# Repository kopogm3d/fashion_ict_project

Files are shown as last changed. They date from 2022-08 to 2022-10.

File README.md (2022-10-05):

# 피팅봇

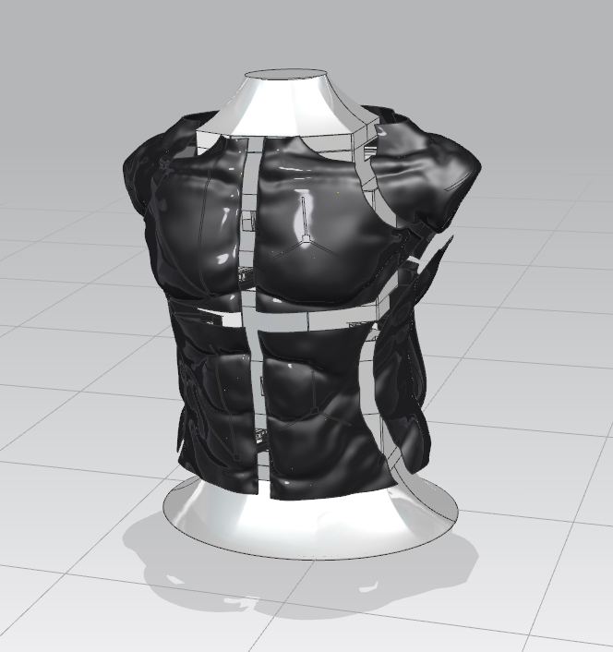
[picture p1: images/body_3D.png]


피팅봇은 하드웨어 기반의 Fashion 산업과 IT 기술 산업의 융합형 project 입니다.

##  개요 

피팅봇은 `스마트 피팅 로봇`으로  인체 치수를 입력하면, 해당 크기로 모습이 변형되는 마네킹입니다. 

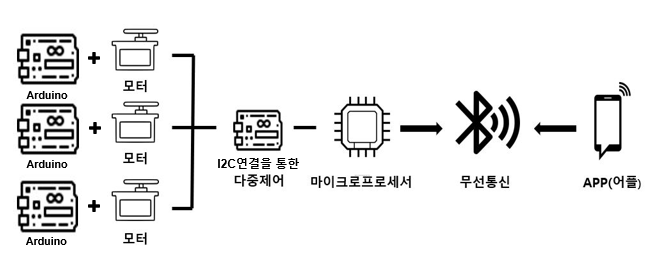
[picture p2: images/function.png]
이미지2


* PRT 모델링 및 STL 출력파일
* 아두이노 Master - Slave 동작코드
* Serial Monitor 및 중앙 제어 시스템

##  주요 제품기능

####  01. 마네킹 기둥설계

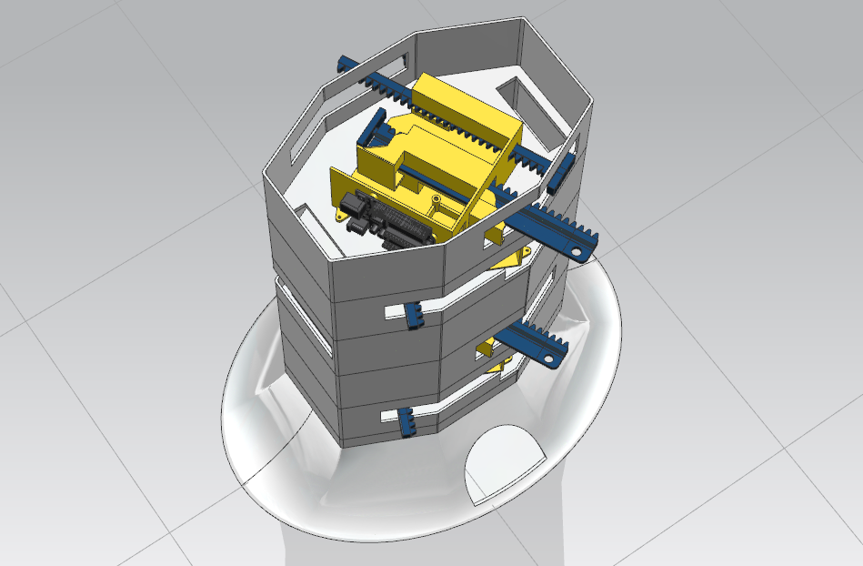
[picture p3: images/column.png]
이미지3

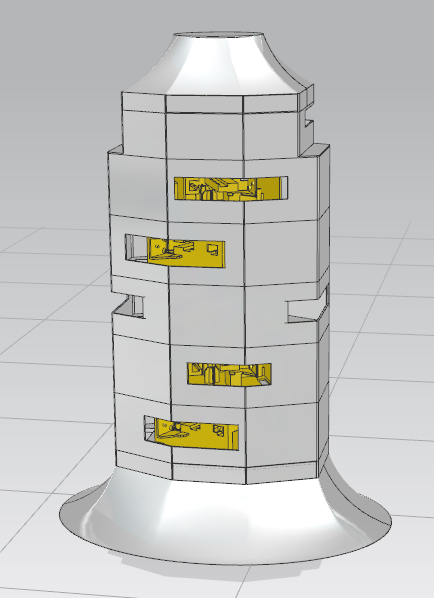
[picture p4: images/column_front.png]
이미지4

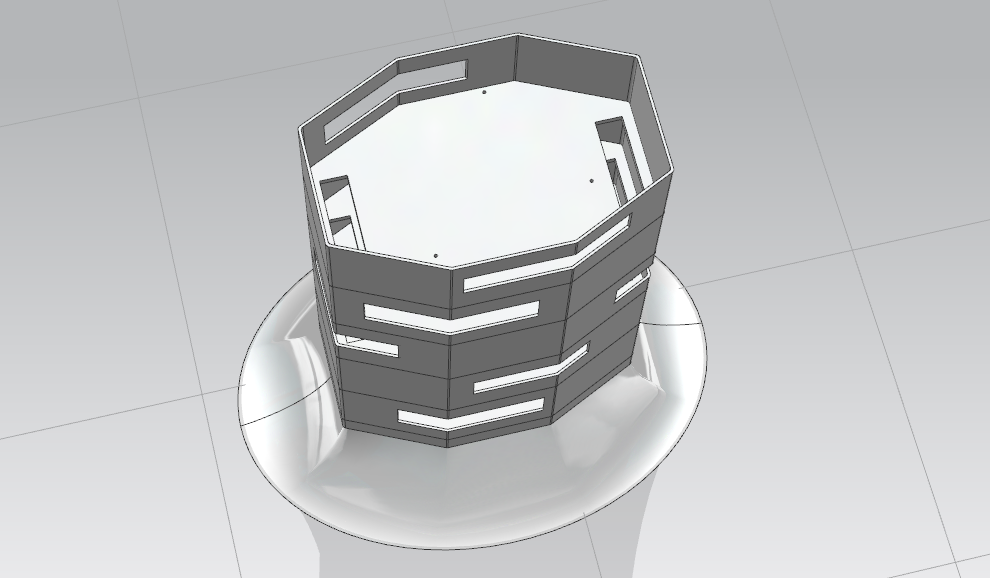
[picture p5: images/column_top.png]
이미지5


6개의 층으로 구성된 기둥을 설계하여 각 층에 모듈을 부착합니다.

####  02. 마네킹 조각 설계

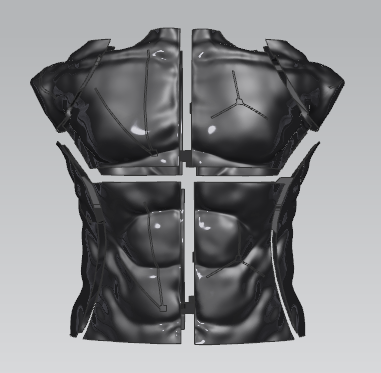
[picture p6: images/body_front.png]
이미지6

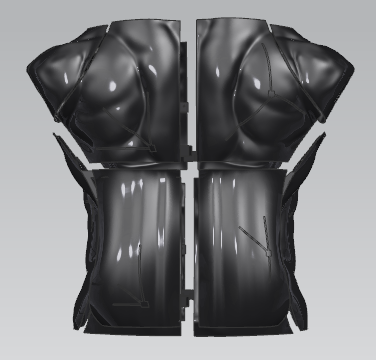
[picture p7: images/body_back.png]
이미지7


신체 형상(상체)은 12 조각으로 나누어 작동시킵니다.

####  03. 랙과 기어 설계

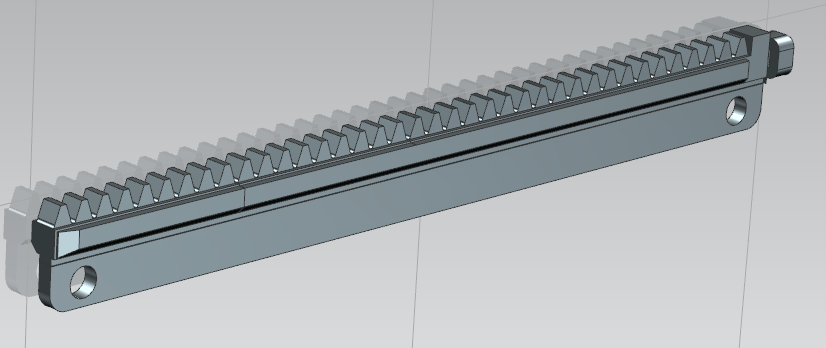
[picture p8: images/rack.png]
이미지8

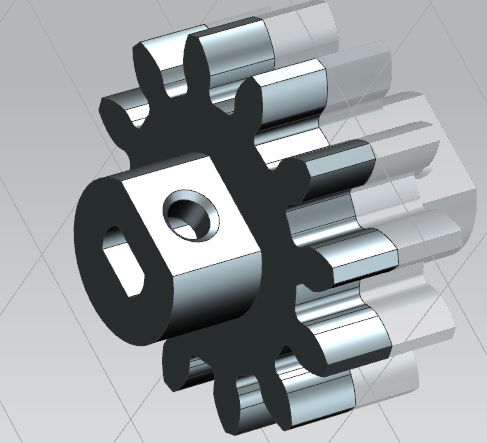
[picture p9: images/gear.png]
이미지9


####  04. 양방향 모듈 설계

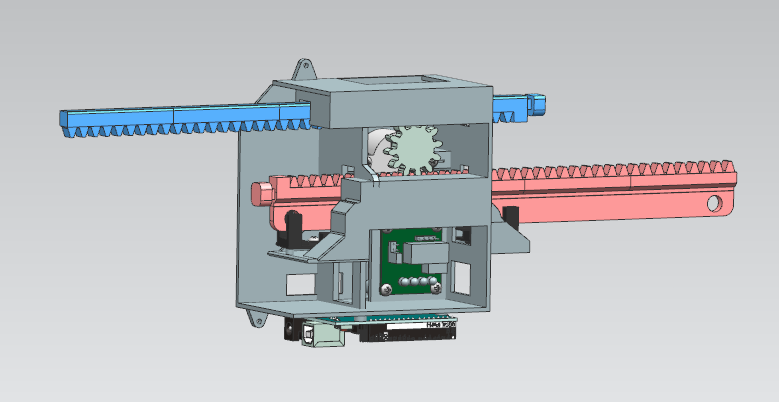
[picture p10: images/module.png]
이미지10

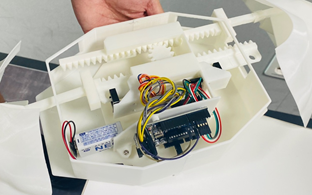
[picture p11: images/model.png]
이미지11


* 스텝모터, 모터 드라이버, 아두이노, 랙과 피니언 기어를 장착시킬 하나의 표준화된 모듈을 설계하여
어떠한 형상의 로봇이든 활용할 수 있습니다.
* 하나의 모터로 두개의 랙 및 조각을 움직일 수 있어 효율적입니다.

####  05. 앱인벤터로 인터페이스 제작

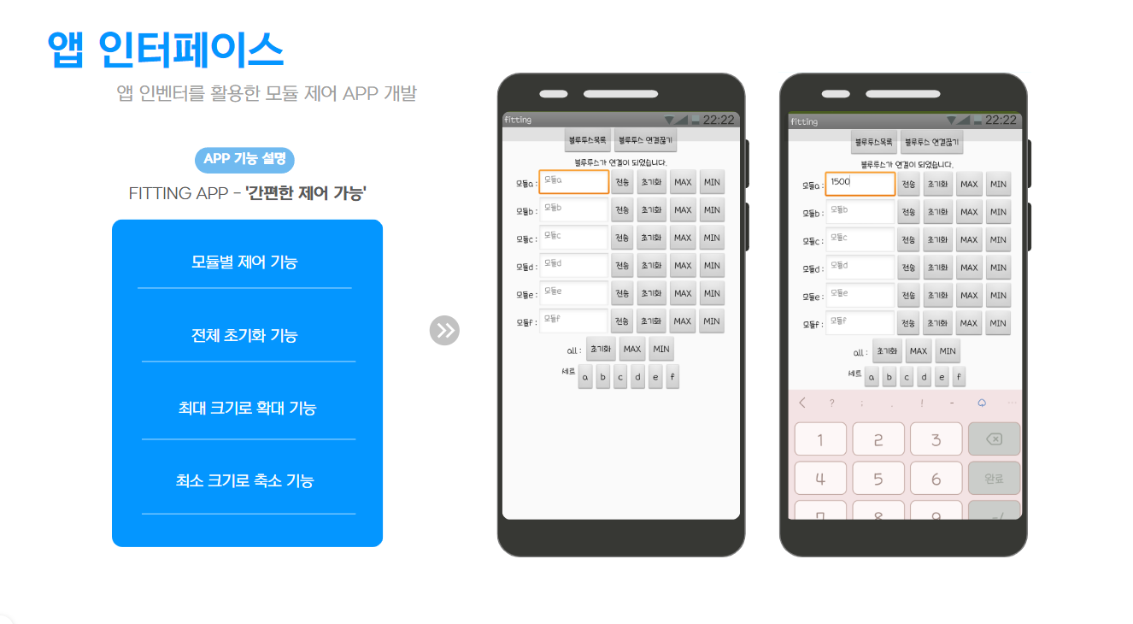
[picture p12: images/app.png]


##### - 앱 사용법
1) 블루투스 목록 및 연결 끊기 기능을 이용해 아두이노와 연결합니다.
2) 모듈을 선택 후 신체 치수를 입력하면 모터가 작동하여 해당 치수만큼 랙이 이동합니다.
3) 최대, 최소 버튼을 이용해 형상을 최대화, 최소화 시킬 수 있습니다.
4) 초기화 버튼을 통해 전체 모듈을 초기값으로 되돌립니다.

##  기술 스택

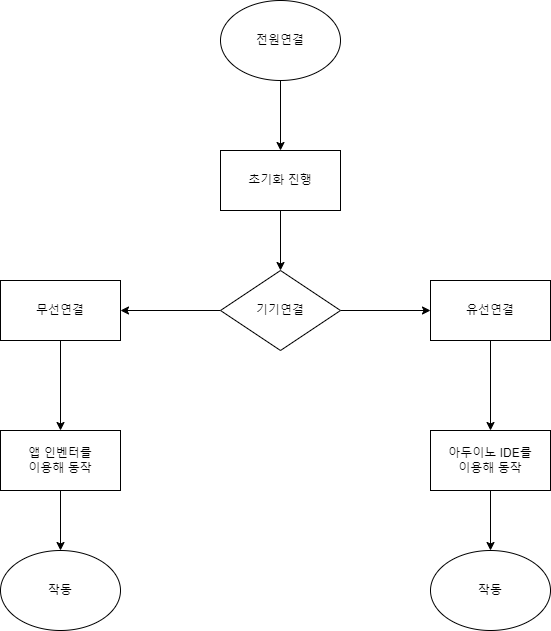
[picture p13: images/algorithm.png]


#####  - 작동 순서

1. 유/무선 연결
-  무선연결 : 블루투스 센서를 이용하여 모바일기기와 연결합니다.
-  유선연결 : 제한된 상황에 대비하여 유선연결을 지원합니다.

2-1. 치수입력
- 사용자가 신체 치수를 입력합니다.
- 유선연결의 경우엔 사용자가 모듈을 선택하는 값을 입력합니다.
- 무선연결 앱 사용자의 경우 미리 정의된 모듈의 텍스트박스 안에 수치를 입력 후 적용버튼을 클릭합니다.

2-2. 저장된 값 불러오기
- 본인이 저장한 수치값을 불러올 수 있습니다.

3. 모터작동
- 불러온 치수데이터를 기반으로 모터를 해당 값만큼 동작시킵니다.

4. 피팅더미의 크기조절
-  모터의 작동을 통해 크기를 축소, 확대 할 수 있습니다.

5. 초기화
-  포토센서를 통한 끝 렉의 끝값을 검출하는 과정을 통해 피팅더미를 초기값으로 되돌립니다.

## 작품 실물 사진

이미지1
이미지1

##### 3D 프린터로 출력한 기둥 및 조각 사진

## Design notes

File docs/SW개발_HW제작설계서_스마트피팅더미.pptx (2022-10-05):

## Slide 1

내가 기획한 ICT가
세상을 바꾼다면?

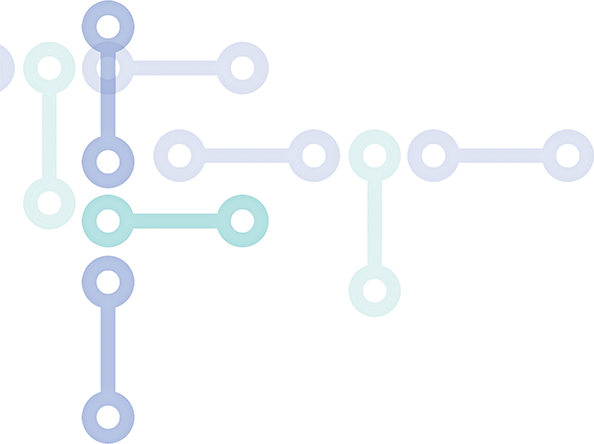
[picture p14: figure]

SW개발/HW제작 설계서

프로젝트 명 : 스마트 피팅 더미

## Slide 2

| 시장/기술 동향 분석

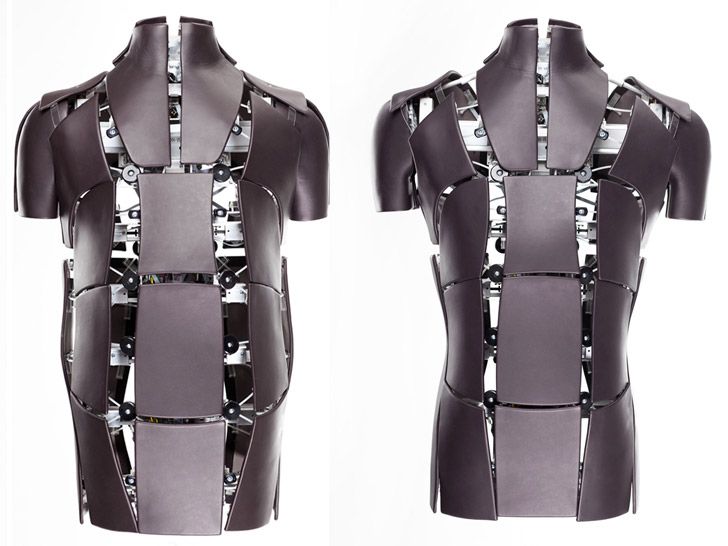
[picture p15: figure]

디자이너가 의류 제작 시 스마트피팅더미 하나만으로 다양한 체형 별 옷사이즈를 직접 눈으로 확인하고 제작할 수 있기에 제작자의 편의를 높임.

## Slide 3

시장/기술 동향 분석

소비자들을 위한 편리한 의류 구매환경 조성 필요

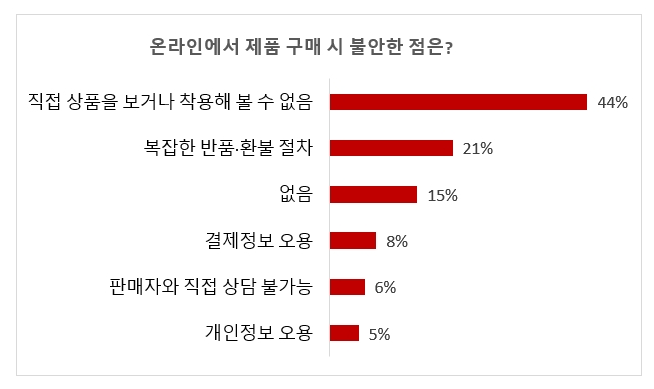
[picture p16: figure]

소비자가 의류 구매 시 매번 직접 착용해볼 수 없기에 불편함을 느낌

디자이너도 의류 제작 시 소비자의 모든 사이즈를
직접 눈으로 확인하는데 불편함이 있음

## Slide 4

| 시장/기술 동향 분석

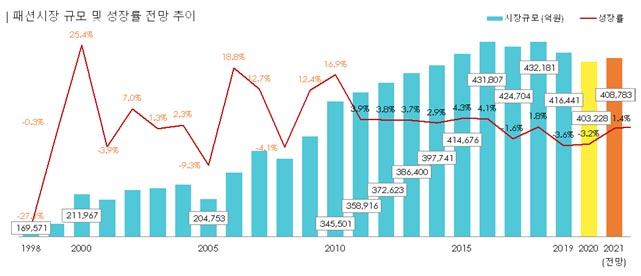
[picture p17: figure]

국내 패션시장의 규모가 점점 성장하고 있으며,
앞으로도 점점 상승할 것으로 전망됨.

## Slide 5

| 요구사항 정의서

구분 | 기능 | 설명
S/W | 수동 치수기입 | 사용자가 입력한 치수를 아두이노로 입력 받는다.
| 해당 수동 치수 저장 | 아두이노로 입력 받은 치수데이터를 저장시킨다.
| 저장된 치수 불러오기 | 저장된 치수 데이터 값을 불러온다.
| 아두이노와 모터간 통신테스트 | 초기화 코드로 통신을 테스트한다. 기반으로 모터를 작동시킨다
| 블루투스 연결을 통한 pc와 피팅더미 통신 | 저장된 치수데이터를 블루투스 기능을 통해 피팅더미를 원격으로 작동시킨다.
| 제한된 상황을 대비한 유선연결 지원 | 무선통신이 안되는 상황을 대비하여 유선연결을 가능하게 한다.

구분 | 기능 | 설명
H/W | 기어,랙 | 사이즈를 최대한 줄인 기어를 사용하고 신체 최대 치수에 맞춘 랙을 사용한다.
| 블루투스 무선통신 | 블루투스 센서를 이용하여 피팅더미와 연결한다.
| 스탭모터 | 360도 회전이 가능한 스탭모터를 사용한다.
| 더미 신체 조각 | 랙과 신체조각을 결합하고, 모터를 통해 랙을 움직여 조각의 위치를 조절한다.
| 아두이노 | 기기로부터 데이터를 송신받아 모터를 움직인다.
| 모터 드라이버 | 아두이노만으로 다량의 모터를 제어하기엔 전력과 포트의 제한이 걸리므로 모터 드라이버를 경유하여 전력을 공급한다.
| SMPS (Switching Mode Power Supply) | 아두이노에 220AC 전력을 12V로 변환시킨다.

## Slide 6

| 시스템 구성도

- 치수 입력
- 사용자의 신체 치수 입력 받는다.
- 유/무선 연결
- 유선이나 블루투스를 통해 아두이노와 사용자기기를 유/무선으로 연결한다.
- 입력 받은 치수 저장
- 저장되어 있는 치수 데이터 값 불러옴
- 저장된 데이터 불러오기
- 저장되어 있는 치수 데이터 값을 불러옴
- 초기화
- 피팅 더미를 초기값으로 되돌린다.
- 치수조절
- 마네킹조각에 연결되어 있는 모터를 이용하여 저장되어 있는 데이터 값을 기반으로 마네킹의 크기를 조절

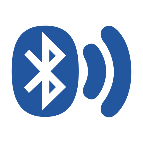
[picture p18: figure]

무선통신

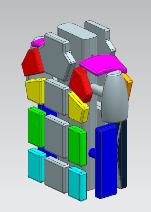
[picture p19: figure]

제작한 마네킹
조각에 모터 부착

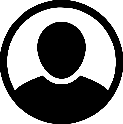
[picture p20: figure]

치수입력

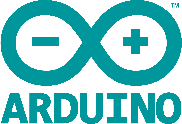
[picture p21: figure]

모터 제어

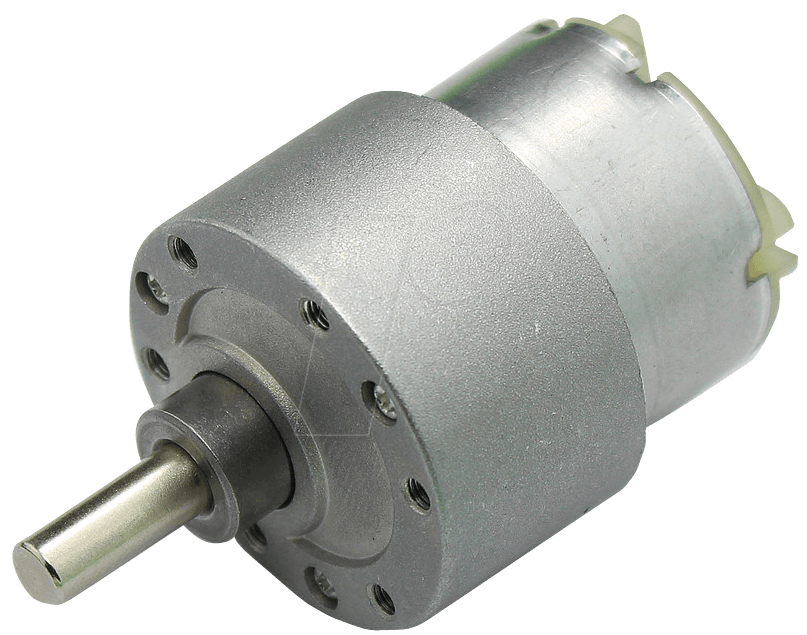
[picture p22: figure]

저장된 치수 불러오기

입력 받은
치수저장

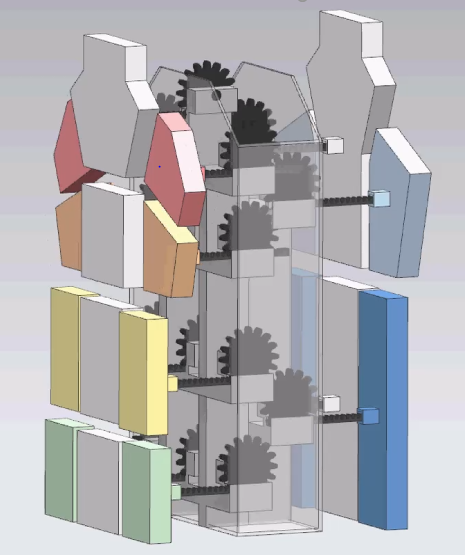
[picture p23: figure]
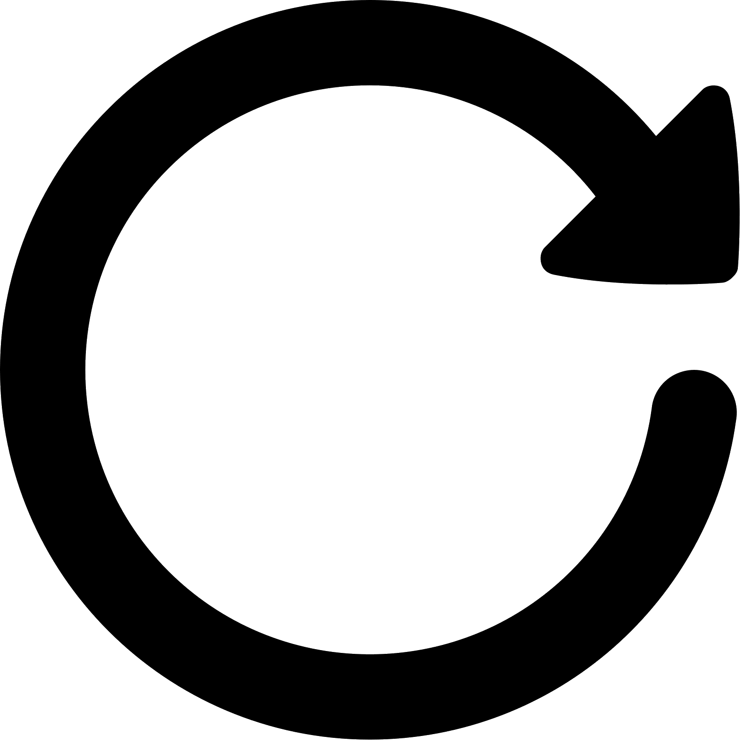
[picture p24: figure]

초기화

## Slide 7

| 하드웨어/센서 구성도

센서종류 | 연결핀 | 설명
Arduino UNO | GND | Step Motor GND에 연결
| VCC | Step Motor VCC에 연결
| Step Motor | Step Motor 신호연결 [2,3,4,5]
| Sensor | Photo Sensor 신호연결 [7,8]
| I2C | 다수기기 통신을 위해 I2C연결 [A4,A5]
| Blue Tooth | 마스터아두이노 블루투스 연결 [2,3]
Step Motor Driver | GND | Arduino – 부 연결
| VCC | Arduino + 부 연결
| Signal | [2,3,4,5] 핀연결
Battery | GND | SMPS – 부 연결
| VCC | SMPS + 부 연결

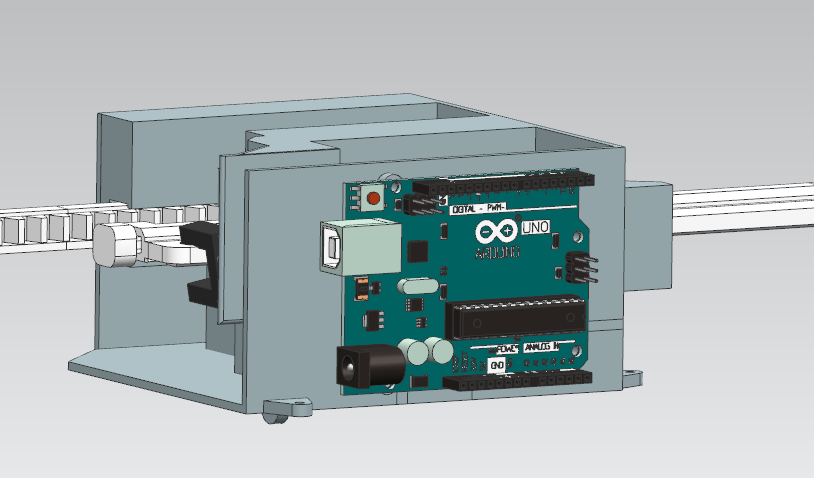
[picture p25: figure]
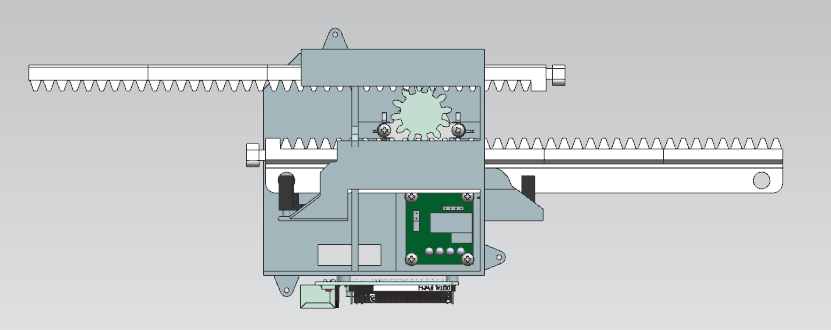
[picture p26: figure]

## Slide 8

| 메뉴 구성도

자동수치

수치입력

수동수치

적용

수치
불러오기

무선
연결

메인 화면

유/무선
연결

기기검색

유선
연결

초기화

초기값으로 적용

웹 연결

웹사이트로 이동

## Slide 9

| UI/UX 정의서 - 화면 설계서

- 제품 사용 프로그램> 수치 입력하기 > 원하는 정보 입력 > 적용

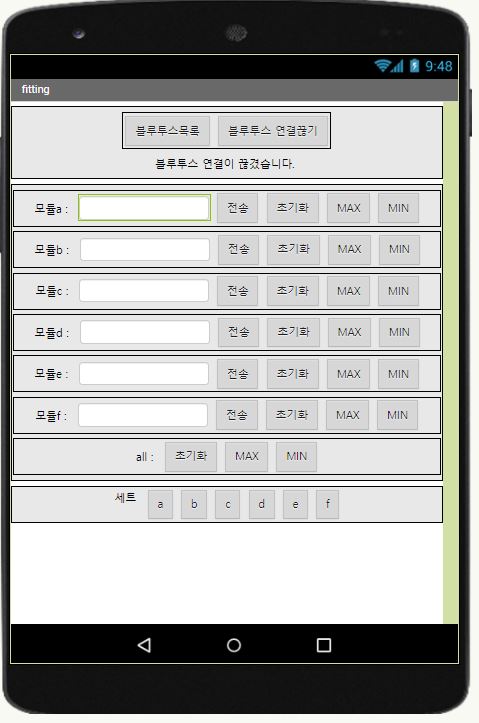
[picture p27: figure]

| 리스트 참고
1 | 평균블루투스 연결하기 연결이 안된 경우 블루투스 목록을 통해 기기를 검색할 수 있고, 연결할 수 있다.
2 | 텍스트박스 텍스트박스에 값을 입력한다.
3 | 모듈동작 전송을 통해 아두이노로 값을 전송하여 모듈을 동작시킨다.
3 | 미리정의된 수치값/ 수치 저장,불러오기 미리 초기화와 최대,최소값을 정의하여 UI화 시켰다. 그외 세트칸에 본인이 원하는 치수를 저장, 불러올 수있다.

[연결이 안된경우 블루투스목록을 통해
기기를 검색하여 연결할 수 있다.]

1

텍스트 박스안에 사용자가
동작하길 원하는 값을 입력할 수 있다.

2

텍스트 입력한 모듈위치의 전송버튼
클릭 시 입력한 값만큼 동작한다.

그외 초기화, 최대값, 최소값을
미리정의하여 지원한다.
아래 세트를 통해 사용자가 원하는
수치를 저장할 수 있다.

3

4

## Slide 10

| 화면 설계서

▶ 기능정보
기능명 | 수치 입력하기
기능설명 | 미리 정의 되어있는 값 이나, 커스텀 값을 통해 모터를 제어 할 수 있다.
처리내용 | 앱이나, 아두이노 시리얼을 통해 모듈을 동작할 수 있다. 텍스트박스에 값을 입력하여 동작할 수 있으며, 수치를 저장,불러오는 것이 가능하다.
관련번호 | -

▶ 사용 예시 정보
| 설명 | 사용자가 동작하길 원하는 수치를 선택하고 전송을 누르면 모듈이 동작한다.
| 입력 데이터 값 | 사용자가 직접 값을 입력할 수 있으며, 값을 저장, 불러올 수 있다. 초기화값과, 최대, 최소값은 미리 정의되어 불러오는 것이 가능하다.

▶ 선행필수기능 및 예외사항
기능명 / 예외사항 | 설명
한 부위만 적용한 경우 | 해당부위만 작동하여 움직인다.
최소/최대값을 초과한 경우 | 최소/최대값을 넘기면 포토센서에 걸려 그 이상 동작하지 않는다.

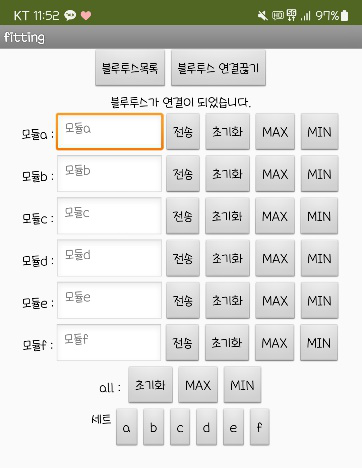
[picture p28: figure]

▶ 입출력 데이터 항목
입출력구분 | 항목 | 설명
입력 | 초기화, 최소 ,최대, 수동입력수치 | 미리 지정해둔 값과, 수동입력 값을 입력
출력 | 기기 작동 | 입력한 수치만큼 모터 작동

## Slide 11

알고리즘 명세서/설명서

실무 산출물 형식

프로그램 ID | - | 프로그램 명 | 모터제어 프로그램 | 작성일 | 22 . 10 . 5 . 수 | Page | -
개요 | 윈도우에서 pc를 통해 이두이노에 값을 입력받고 아두이노에서 모터에 신호를 보내 피팅더미를 움직인다. | | | | | 작성자 | 이동희

1. 유/무선 연결
- 무선연결 : 블루투스 센서를 이용하여 모바일기기와 연결한다.
- 유선연결 : 제한된 상황에 대비해. 유선연결을 지원한다.
2-1. 치수입력
- 사용자가 신체 치수를 입력한다.
- 유선연결의 경우엔 사용자가 모듈을 선택하는 값을 입력해준다.
- 무선연결 앱 사용자의 경우 미리 정의된 모듈의 텍스트박스 안에 수치를 입력 후 적용버튼을 누른다.
2-2. 저장된 값 불러오기
- 본인이 저장한 수치값을 불러올 수 있다.
3. 모터작동
- 불러온 치수데이터를 기반으로 모터를 해당 값만큼 동작시킨다.
4. 피팅더미의 크기조절
- 모터의 작동을 통해 크기를 축소, 확대 할 수 있다.
5. 초기화
- 포토센서를 통한 랙의 끝값을 검출하는 과정을 통해 피팅더미를 초기값으로 되돌린다.


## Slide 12

| 기능 처리도(기능 흐름도)

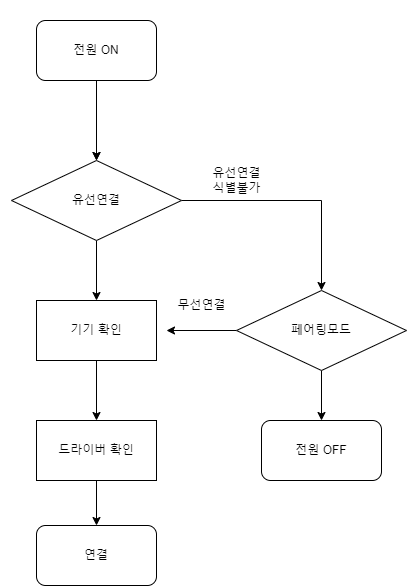
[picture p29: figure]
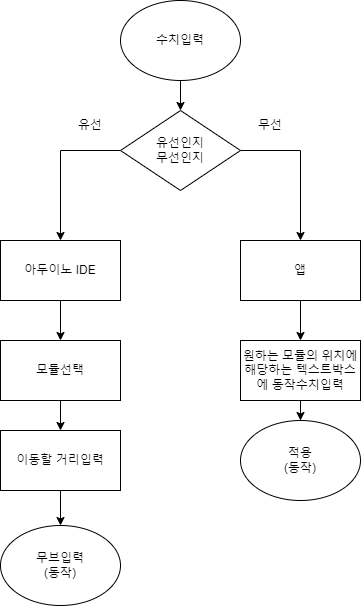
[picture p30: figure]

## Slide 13

| 핵심소스코드

2

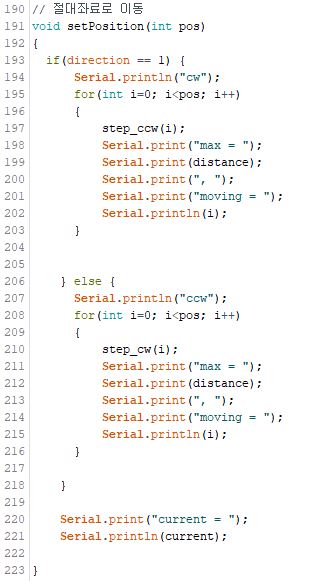
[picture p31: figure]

3

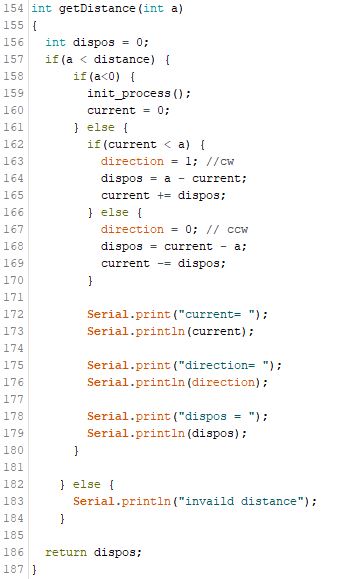
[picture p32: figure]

1.모듈선택소스코드(ASCII)
2.값을 입력받는 코드
3.입력된 값으로 모터에 전송

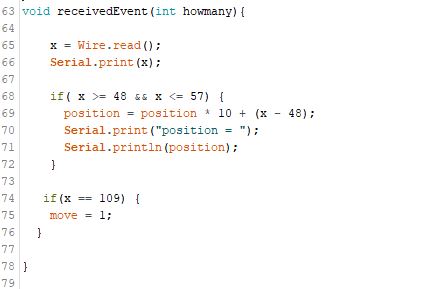
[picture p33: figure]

1

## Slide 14

| 프로그램 - 목록

기능 분류 | 기능번호 | 기능 명
PWR (POWER) | PWR-01 | 전원 ON
| PWR-02-01 | 유선연결
| PWR-02-02 | 페어링모드
| PWR-03 | 기기확인
| PWR-04-01 | 연결
| PWR-04-02 | 전원 OFF
FVR (FAVORITE) | FVR-01-01 | ALL – 초기화
| FVR-01-02 | ALL – MAX
| FVR-01-03 | ALL – MIN
A_MD (A-module) | A_MD-01-01 | A - 전송
| A_MD-01-02 | A – 초기화

한이음 ▶ 프로그램 설계서

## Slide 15

| 참조- 개발 환경 및 설명

구분 | | 항목 | 적용내역
S/W 개발환경 | 윈도우/안드로이드/IOS 조작 프로그램 개발 | App Inventor | 윈도우/안드로이드/IOS에서 수치값을 입력받는 프로그램 개발을 위해 사용한다.
| 아두이노 동작 프로그램 개발 | Arduino | 피팅더미 내부의 아두이노를 실행시키기 위해 사용한다.
| 에뮬레이션 프로그램 | Remote Testkit | 다양한 앱 환경에서 사용시 호환성 테스트를 위해 사용한다.
H/W 구성장비 | 아두이노 | 피팅더미 통신디바이스 (SZH-EK080) | 피팅더미 내부의 아두이노를 통해 모터를 동작한다.
| 스탭모터 | 조각이동을 위한 모터 (28byj) | 아두이노로 부터 값을 받아서 모터를 동작하여 랙을 동작인다.
| 모터 드라이버 | 다수의 모터제어 (ULN2003) | 대량의 모터가 들어감으로 모터드라이버를 경유하여 전력을 공급한다.
| 블루투스 송-수신기 | 블루투스 통신모듈 (SZH-EK105) | 아두이노에 블루투스 기능을 추가하여 다양한 기기와 통신을 가능하게 한다.
| 기어 & 랙 | 자체 제작 및 생산 예정 | 랙과 기어를 이용하여 피팅더미 조각을 움직인다.

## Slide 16

내가 기획한 ICT가
세상을 바꾼다면?

Thank you

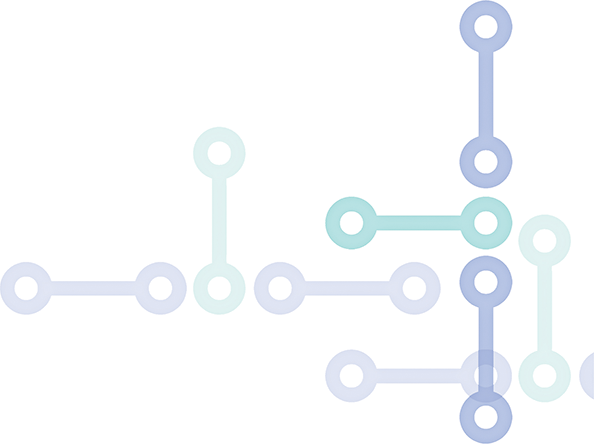
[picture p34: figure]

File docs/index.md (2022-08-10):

# 프로젝트

## 일정관리

[일정관리](https://docs.google.com/spreadsheets/d/1b1e-LViBpw9x0WHoBi6NbNIejE0as57JXm7uGB9Ble4/edit?usp=sharing)
[공유문서](https://drive.google.com/drive/folders/1tGMNQquNc3pgP5mi_j5m_SsK1CPc5LEh?usp=sharing)

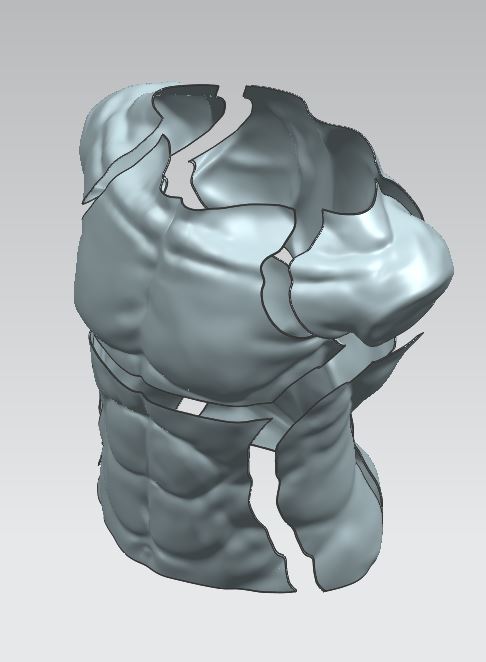
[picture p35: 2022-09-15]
images/piece.JPG

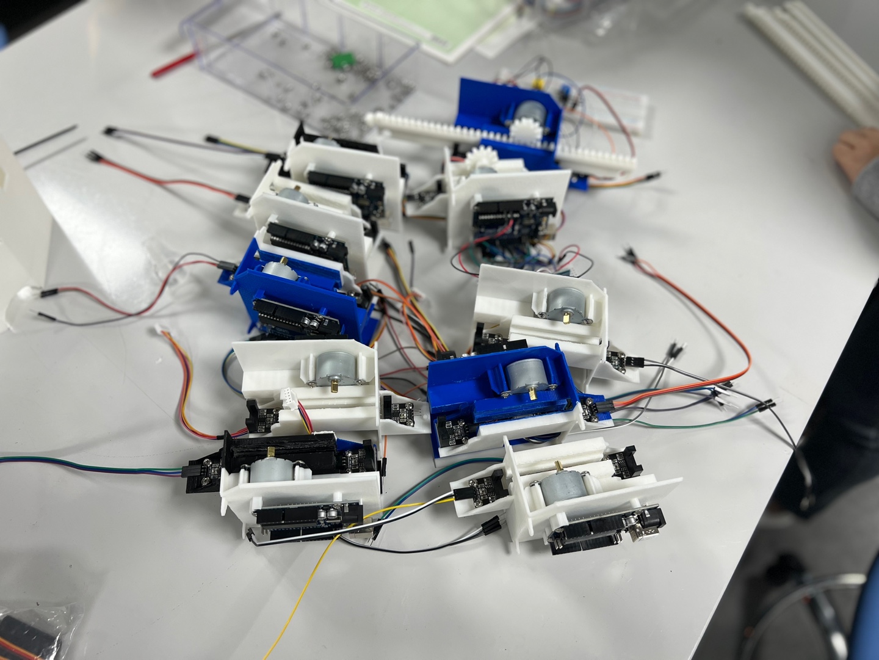
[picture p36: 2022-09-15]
images/KakaoTalk_20220906_184110311_02.jpg

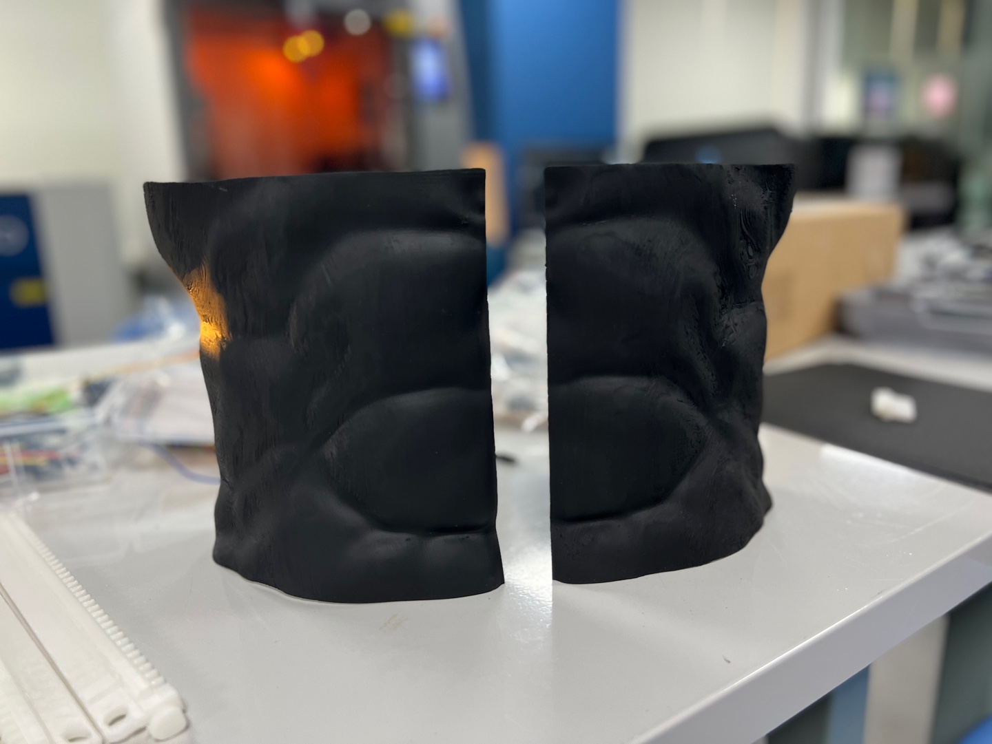
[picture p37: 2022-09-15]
images/KakaoTalk_20220906_184110311.jpg

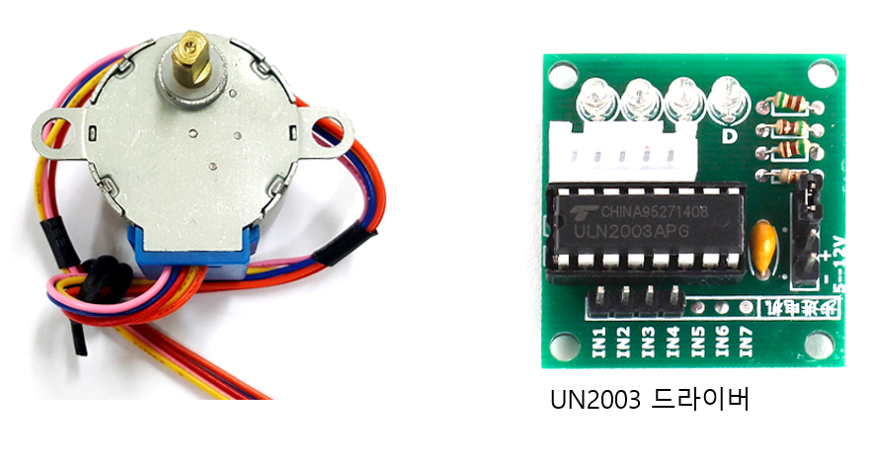
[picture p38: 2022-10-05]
images/stepmotor.png

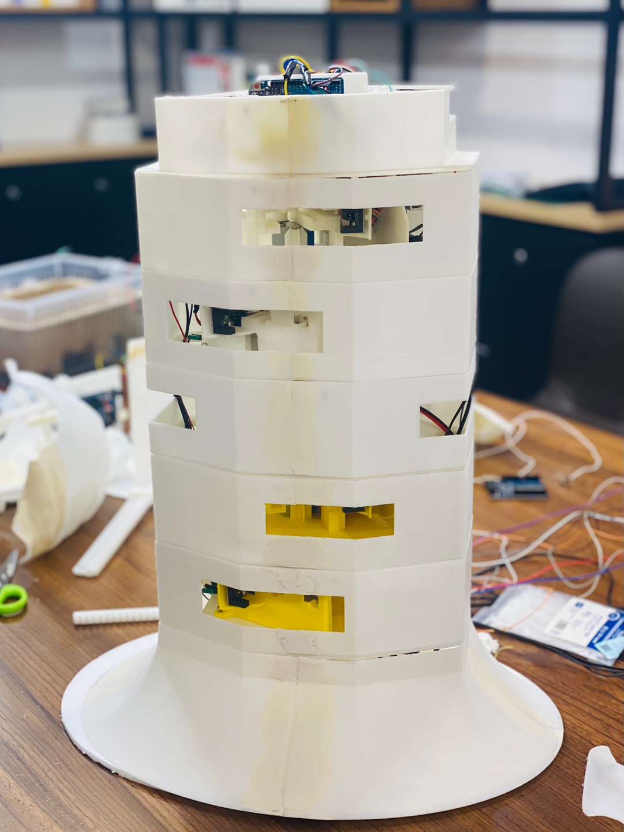
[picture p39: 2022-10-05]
images/column_new.jpg

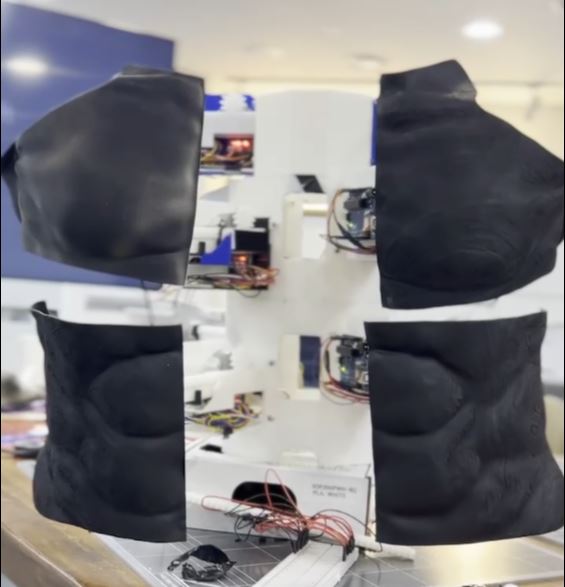
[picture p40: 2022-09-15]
images/캡처.JPG

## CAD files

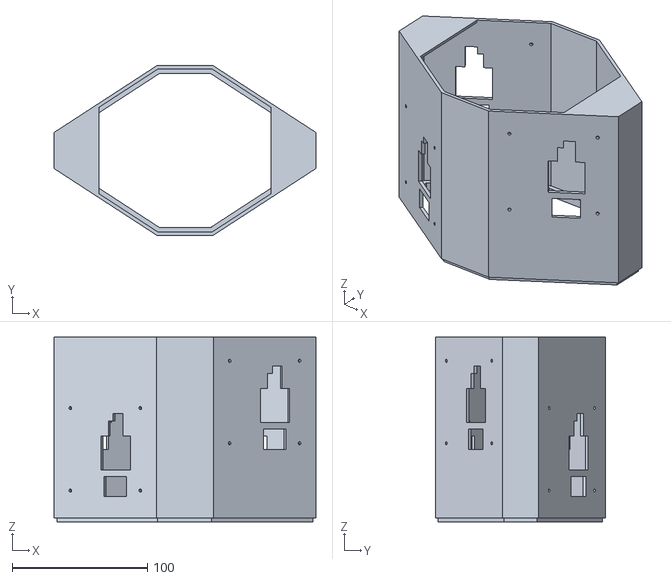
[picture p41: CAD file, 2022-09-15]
modeling/stl/기둥2층.stl
193.8 x 125.4 x 136.6

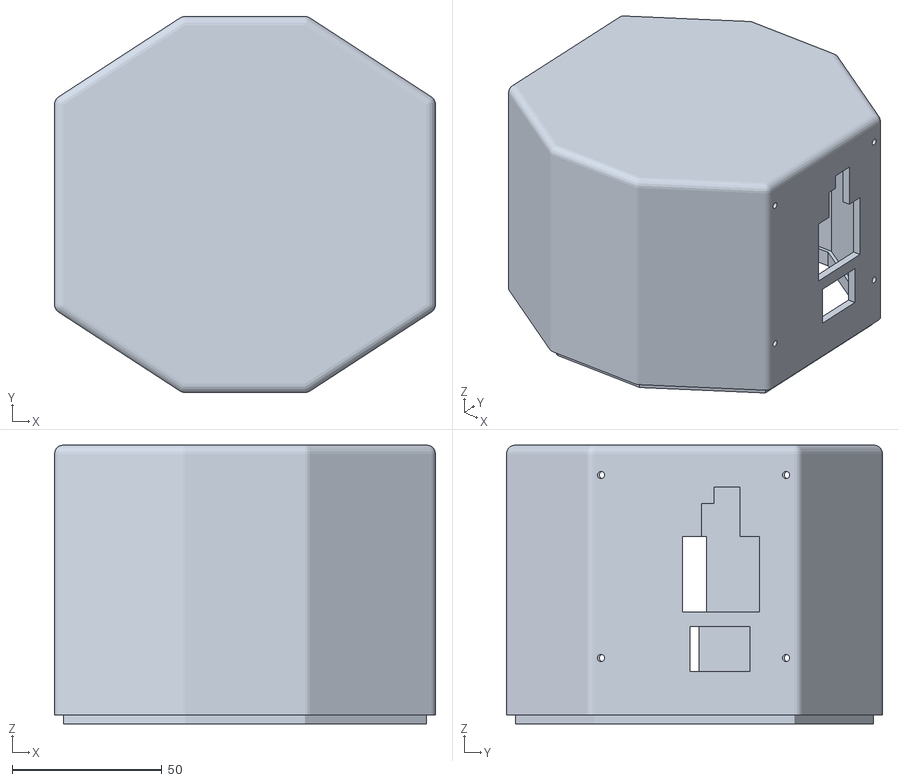
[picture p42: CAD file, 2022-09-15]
modeling/stl/기둥3층.stl
127.0 x 125.4 x 93.0

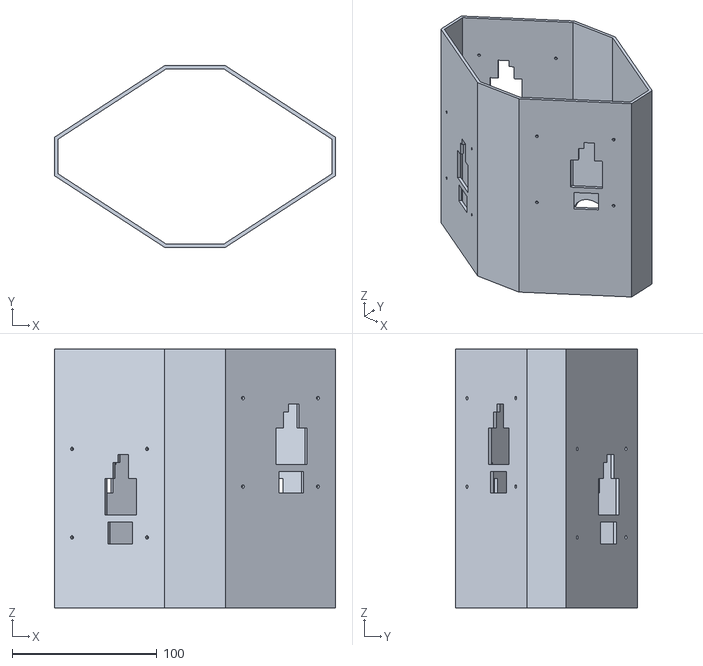
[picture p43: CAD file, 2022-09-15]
modeling/stl/기둥1층.stl
193.8 x 125.4 x 178.6

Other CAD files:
modeling/prt/new 어깨1.prt
modeling/prt/new 어깨2.prt
modeling/prt/모듈 합본.prt
modeling/prt/모듈.prt
modeling/prt/옆구리1.prt
modeling/prt/옆구리2.prt

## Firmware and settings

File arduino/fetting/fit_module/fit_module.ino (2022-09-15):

#include <Wire.h>

#define motorPin1 2 // IN1
#define motorPin2 3 // IN2
#define motorPin3 4 // IN3
#define motorPin4 5 // IN4
 
#define step 2048 // 1봐퀴 스텝수

// 모터 회전 Loop 문 구현을 간단하게 하기위해 핀 배열 선언
int pinArray[4] = { motorPin1, motorPin2, motorPin3, motorPin4 };

// CW 시계방향 데이터 전송
int CW[4] = {0b1000,0b0100,0b0010,0b0001};
int CCW[4] = {0b0001,0b0010,0b0100,0b1000};

int step_count = 0;
int distance = 0;

const int beepPin = 12;

const int i2c = 1;

int x = 0;
int position = 0;

int move = 0;

void initBeep()
{
  pinMode(beepPin, OUTPUT);
  beep();
}

void beep()
{
  digitalWrite(beepPin, HIGH);
  delay(70);
  digitalWrite(beepPin, LOW);
}

void setup(){
  // 핀모드 설정
  // 스텝모터 드라이브 보드의 IN 연결핀 출력으로 설정
  for(int i = 0 ; i < 4 ; i++ ) {
    pinMode(pinArray[i], OUTPUT);
  }

  // 시리얼 초기화
  Serial.begin(115200);
  Serial.println("module start");

  Wire.begin(i2c); // ic2 초기화
  Wire.onReceive(receivedEvent);

  // Beep
  initBeep();

  // 초기화 동작
  init_process();
}

void receivedEvent(int howmany){

    x = Wire.read();
    Serial.print(x);
    
    if( x >= 48 && x <= 57) {
      position = position * 10 + (x - 48);
      Serial.print("position = ");
      Serial.println(position);
    }

   if(x == 109) {
    move = 1;
  }

}

int max_detact()
{
  int status = digitalRead(7);
  if(status == LOW){
    return 1; // 끝 검출
  } else {
    return 0; // 동작가능한 범위
  }
}

int min_detact()
{
  int status = digitalRead(8);
  if(status == LOW){
    return 1; // 끝 검출
  } else {
    return 0; // 동작가능한 범위
  }
}

int direction = 1; // 역방향 : 0

int btn_up()
{
  int btn_sw1 = digitalRead(9);
  if(btn_sw1 == LOW){
    return 1;
  } else {
    return 0;
  }
}

int btn_down()
{
  int btn_sw1 = digitalRead(10);
  if(btn_sw1 == LOW){
    return 1;
  } else {
    return 0;
  }
}

int current = 0;

void loop() {
  int a = 0;
  int d = 0;
  if(Serial.available()){
    a = Serial.parseInt();
    Serial.println(a);
    //d = getDistance(a);
    position = a;
    move = 1;
  }

  if(position>0) {
    if(move == 1) {
      d = getDistance(position);
      position = 0; // 초기화
      move = 0;
    }
    
  }

  

  if(d>0) {
    setPosition(d); // 절대 좌표로 이동
    beep();
    d = 0;
  }

}

int getDistance(int a)
{
  int dispos = 0;
  if(a < distance) {
      if(a<0) {
        init_process();
        current = 0;
      } else {       
        if(current < a) {
          direction = 1; //cw
          dispos = a - current;
          current += dispos;
        } else {
          direction = 0; // ccw
          dispos = current - a; 
          current -= dispos;     
        }
    
        Serial.print("current= ");
        Serial.println(current);
      
        Serial.print("direction= ");
        Serial.println(direction);
    
        Serial.print("dispos = ");
        Serial.println(dispos);
      }
      
    } else {
      Serial.println("invaild distance");
    } 

  return dispos;
}


// 절대좌료로 이동
void setPosition(int pos)
{
  if(direction == 1) {
      Serial.println("cw");
      for(int i=0; i<pos; i++)
      {
          step_ccw(i);
          Serial.print("max = ");
          Serial.print(distance);
          Serial.print(", ");
          Serial.print("moving = ");
          Serial.println(i);
      }      

 
    } else {
      Serial.println("ccw");
      for(int i=0; i<pos; i++)
      {
          step_cw(i);
          Serial.print("max = ");
          Serial.print(distance);
          Serial.print(", ");
          Serial.print("moving = ");
          Serial.println(i);
      }

    }

    Serial.print("current = ");
    Serial.println(current);

}

void gear_loop()
{
  if(direction == 1 && min_detact()){
    step_count=0;
  }

  if(direction == 0 && max_detact()){
    step_count=0;
  }
  
  if(max_detact()) {
    // 모터 동작
    Serial.println("ccw working");
    direction = 1;
    
  } else if(min_detact()){
    // 모터 동작
    Serial.println("cw working");
    direction = 0;
  
  }

  if(direction == 0) {
      step_count++;
      //step_ccw();

  } else {
      step_count++;
      //step_cw();
  }

  Serial.println(step_count);
}








void init_process()
{
  // 앞방향 최대치 검사
  move_to_max();

  distance = 0;
  delay(1000);
  
  // 뒤방향 최소치 검사 
  distance = move_to_min();
  
  Serial.print("gear distance = ");
  Serial.println(distance);

}


int move_to_max()
{
  Serial.println("checking max");
  int temp, i=0;
  while(!max_detact()){
    temp = i++ % 4;
    digitalWrite(pinArray[0], bitRead(CCW[temp], 0));
    digitalWrite(pinArray[1], bitRead(CCW[temp], 1));
        digitalWrite(pinArray[2], bitRead(CCW[temp], 2));
        digitalWrite(pinArray[3], bitRead(CCW[temp], 3));
        stepDelay();
  }
  return i;
}

int move_to_min()
{
  Serial.println("checking min");
  int temp, i=0;
  while(!min_detact()){
    temp = i++ % 4;
    digitalWrite(pinArray[0], bitRead(CW[temp], 0));
    digitalWrite(pinArray[1], bitRead(CW[temp], 1));
    digitalWrite(pinArray[2], bitRead(CW[temp], 2));
    digitalWrite(pinArray[3], bitRead(CW[temp], 3));
    stepDelay();
  }

  return i;
}



void step_cw(int count)
{
  int temp;
  temp = count % 4;
  digitalWrite(pinArray[0], bitRead(CW[temp], 0));
  digitalWrite(pinArray[1], bitRead(CW[temp], 1));
  digitalWrite(pinArray[2], bitRead(CW[temp], 2));
  digitalWrite(pinArray[3], bitRead(CW[temp], 3));
  stepDelay();
  // Serial.println("cw");
}

void step_ccw(int count)
{
  int temp;
  temp = count % 4;
  digitalWrite(pinArray[0], bitRead(CCW[temp], 0));
  digitalWrite(pinArray[1], bitRead(CCW[temp], 1));
  digitalWrite(pinArray[2], bitRead(CCW[temp], 2));
  digitalWrite(pinArray[3], bitRead(CCW[temp], 3));
  stepDelay();
  // Serial.println("ccw");
}

void stepDelay()
{
  // 모터 부하가 없는 상태에서, 
  // 각 스텝 간격이 최소 3ms 이상이어야 정상적으로 동작합니다.
  delay(3);
}

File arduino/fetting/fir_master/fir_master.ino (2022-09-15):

#include <Wire.h>
/*
const int button1 = 8;
const int button2 = 9;

int x = 0;
int y = 0;
*/

const int beep = 12;

void initBeep()
{
  pinMode(beep, OUTPUT);
  
  digitalWrite(beep, HIGH);
  delay(70);
  digitalWrite(beep, LOW);
  delay(70);
  digitalWrite(beep, HIGH);
  delay(70);
  digitalWrite(beep, LOW);
}

void setup()
{
  Wire.begin(); // i2c 통신
  Serial.begin(115200); // 시리얼 통신

  initBeep();
  
  Serial.println("start");
}

int module = 0; // 0: 선택하지 않음
int position = 0;
int exponent = 0; // 숫자 승수

void loop()
{
  int position = 0;
  if(Serial.available()){
    char a = Serial.read();
    if(a >= 'a' && a <= 'j') {
      Serial.print("select module = ");
        Serial.println(a);
        module = a-96; // 모듈 선택 저장
    }
    
    if(a == '-') {
      Serial.println("init...");
        module = 0;
    }
    
    if(a >= '0' && a <= '9') {
      Serial.print("position = ");
      //Serial.print(a);
      
      position = position * 10 + (a - '0');
      Serial.println(position);
      
      selectModule( module, a);
    }

    if(a == 'm') {
      selectModule( module, 'm');
      Serial.print("move = ");
      Serial.print(a);
    }
    
  }
 
}




void selectModule(int m, int value)
{
  Wire.beginTransmission(m);
    Wire.write(value);
    Wire.endTransmission();
}

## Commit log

2022-08-10 일정관리
2022-08-10 구글문서
2022-09-15 modeling prt
    [new 어깨1.prt, new 어깨2.prt, 모듈 합본.prt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]
2022-09-15 stl 3d printing
    [기둥1층.stl, 기둥2층.stl, 기둥3층.stl]
2022-09-15 arduino code
